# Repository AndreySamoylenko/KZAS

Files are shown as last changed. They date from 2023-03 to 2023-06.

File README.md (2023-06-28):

# О содержании репозитория

В папке [технический журнал](https://github.com/AndreySamoylenko/KZAS/blob/main/технический%20журнал) находятся три документа, в них рассмотрено устройство робота и логика прохождения трассы. 

В файле [Обсуждение системы перемещения.pdf](https://github.com/AndreySamoylenko/KZAS/blob/main/технический%20журнал/Обсуждение%20системы%20перемещения.pdf) рассмотрены некоторые 3D модели и их назначение, а также некоторые аспекты выбора комплектующих.

В файле [Обсуждение системы питания и сенсоров.pdf](https://github.com/AndreySamoylenko/KZAS/blob/main/технический%20журнал/Обсуждение%20системы%20питания%20и%20сенсоров.pdf) представлены сравнения электрических компонентов, и объяснён выбор тех моделей которые вошли в конечную схему. В этом же файле вы можете ознакомиться с логической и принципиальной схемами, которые показывают взаимодействия компонентов и устройство электрической схемы робота.

В файле [Обсуждение системы распознавания препятствий.pdf](https://github.com/AndreySamoylenko/KZAS/blob/main/технический%20журнал/Обсуждение%20систем%20распознавания%20препятствий.pdf) показаны и разобраны некоторые алгоритмы, и объяснены части кода программ из папки [программы](https://github.com/AndreySamoylenko/KZAS/blob/main/программы). В этом документе разобраны только программы отвечающие за распознавание препятствий.

Папка [программы](https://github.com/AndreySamoylenko/KZAS/blob/main/программы) содержит все программы использованные нами в процессе разработки

В папке [видео](https://github.com/AndreySamoylenko/KZAS/blob/main/видео) находится текстовый файл со ссылкой на видео.

Папка  [Фотографии робота](https://github.com/AndreySamoylenko/KZAS/blob/main/Фотографии%20робота) содержит 11 фотографий, 10 фотографий робота и 1 фото команды.

В папке [3D модели](https://github.com/AndreySamoylenko/KZAS/blob/main/3D%20модели) вы можете найти все 3д модели деталей, которые мы печатали.

# Пояснения к программам 

Здесь будет представлено краткое описание программ.

[RobotAPI.py](https://github.com/AndreySamoylenko/KZAS/blob/main/программы/RobotAPI.py) - это класс используемый программой [start_robot.py](https://github.com/AndreySamoylenko/KZAS/blob/main/программы/start_robot.py). Он необходим для загрузки программы на распберри, и получения изображения с камеры по Wi-Fi.

[start_robot.py](https://github.com/AndreySamoylenko/KZAS/blob/main/программы/start_robot.py) - это программа создающая удобный интерфейс для взаимодействия с роботом (фотка). Использование этой программы будет рассмотрено подробно в разделе "подключение к распберри".

[main.py](https://github.com/AndreySamoylenko/KZAS/blob/main/программы/main.py) - это программа, исполняемая микроконтроллером. 
Сама программа выглядит примерно так: 
1) принять сообщение от raspberry  
2) расшифровать его и получить целевой угол сервопривода, скорость мотора и цвет RGB светодиода
3) зажечь светодиод нужным цветом
4) запустить мотор с нужной скоростью
5) повернуть сервопривод на целевой угол
6) повторить

Программы [qualification](https://github.com/AndreySamoylenko/KZAS/blob/main/программы/qualification.py), [final.py](https://github.com/AndreySamoylenko/KZAS/blob/main/программы/final.py) загружаются на raspberry pi с помощью [start_robot.py](https://github.com/AndreySamoylenko/KZAS/blob/main/программы/start_robot.py), и имеют схожую структуру. 

Все их можно разделить на 3 этапа работы (в программе этапы определяются переменной "state"): 

1) ожидание нажатия кнопки (state == 0)
2) прохождение трассы (state == 1)
3) остановка (state == 3)

(когда state == 2 робот проходит последние ползоны, чтобы финишировать в центре) 

На первом этапе raspberry отправляет сообщение "999999999999999999999$", которое pyboard получает и ждет изменения значения, параллельно отправляя показания кнопки. 

Когда кнопка нажата, pyboard отсылает сообщение: "1$". 
raspberry получает это сообщение и начинает движение.   

В [qualification](https://github.com/AndreySamoylenko/KZAS/blob/main/программы/qualification.py), второй этап - прохождение трассы с помощью пропорционально-дифференциального регулятора с двумя датчиками и с параллельным считыванием так называемых перекрёстков (оранжевая и синяя линии). 

ПД регулятор сначала вычисляет отклонение (e=dat1-dat2) исходя из показаний датчиков бортика, а затем на его основе вычисляет управляющее воздействие (u = (e * kp + (e - e_old) * kd))  (e_old - предыдущее отклонение). 

[final.py](https://github.com/AndreySamoylenko/KZAS/blob/main/программы/final.py) работает иначе - в него добавлены функции избегания знаков. 

На кадре появляется большой датчик, который ищет знаки и возвращают их цвет и координаты на кадре, а также, в программе появляется новый ПД регулятор, и если робот замечает знак, то вычисляет новое отклонение относительно этого знака, игнорируя черные линии и используя специальный ПД регулятор для знаков. 
Также для более быстрого прохождения трассы мы добавили функцию разгона, то есть когда робот не видит знаков, его скорость растёт, а когда знак появляется на кадре скорость падает.

Также в папке [программы](https://github.com/AndreySamoylenko/KZAS/blob/main/программы) есть файл [autostart.py](https://github.com/AndreySamoylenko/KZAS/blob/main/программы/autostart.py), в этот файл вы можете импортировать программу, которую робот будет выполнять при запуске.

# Подключение к pyboard 

Для подключения к pyboard необходимо с помощью micro usb кабеля подключить pyboard к компьютеру. После этого в проводнике появится устройство с названием PYBFLASH. 

На этом устройстве будут два файла main.py и boot.py. Файл [main.py](https://github.com/AndreySamoylenko/KZAS/blob/main/программы/main.py) - это та программа, которую будет исполнять pyboard. 

Вы можете скопировать её в свою среду разработки и изменить, если это необходимо, после этого вам нужно заменить файл [main.py](https://github.com/AndreySamoylenko/KZAS/blob/main/программы/main.py) в папке PYBFLASH на отредактированный, и после того как погаснет красный светодиод нужно будет нажать на кнопку RESET (RST). 
После этого pyboard перезагрузится и начнёт выполнение программы [main.py](https://github.com/AndreySamoylenko/KZAS/blob/main/программы/main.py)
  
# Подключение к raspberry pi 

Сначала вам нужно включить питание робота (или подключить питание распберри отдельно) и подождать какое-то время, это нужно для того чтобы на распберри запустилась операционная система, и включилась точка доступа. 
После этого ищем сеть нашей raspberry и подключаемся к ней.

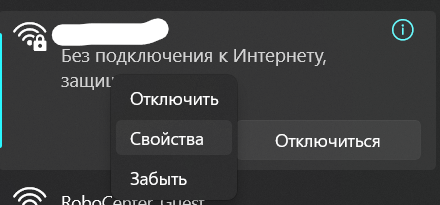
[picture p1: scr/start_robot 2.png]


Нажимаем "свойства" и ищем пункт "IPv4".

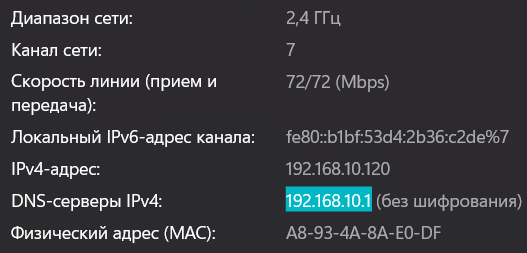
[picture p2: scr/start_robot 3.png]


После этого копируем это IP адрес и вставляем его в [start_robot.py](https://github.com/AndreySamoylenko/KZAS/blob/main/программы/start_robot.py) как на фото.

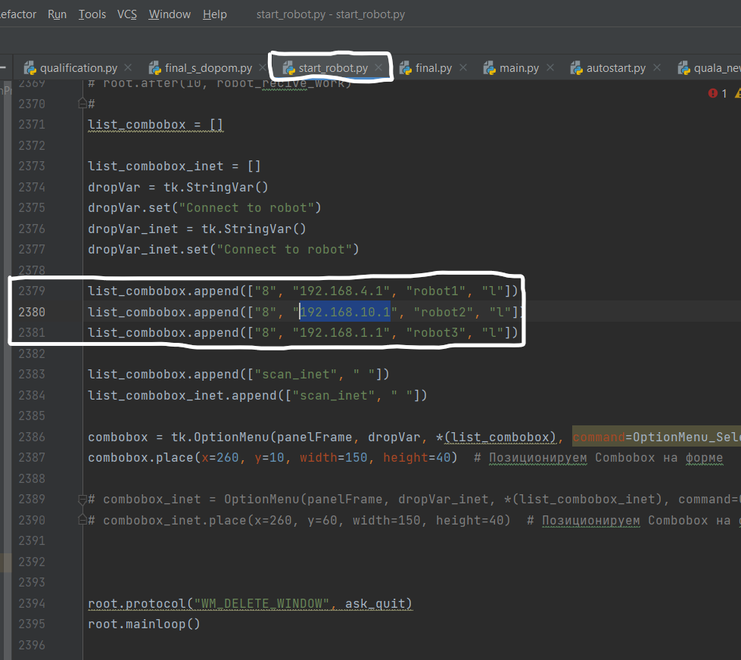
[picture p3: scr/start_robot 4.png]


здесь же можно изменить подпись, которая будет отображаться в выпадающем меню.

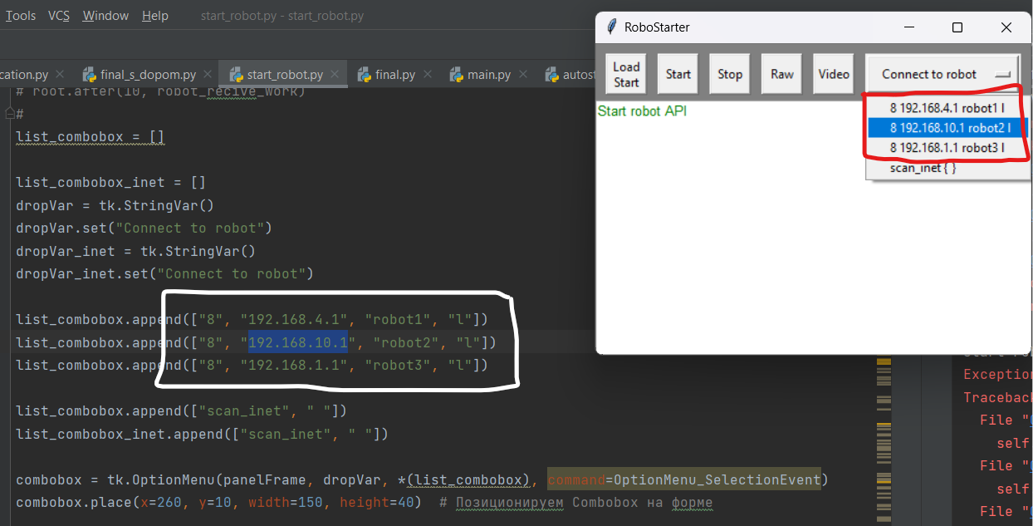
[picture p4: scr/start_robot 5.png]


После этого перезапускаем [start_robot.py](https://github.com/AndreySamoylenko/KZAS/blob/main/программы/start_robot.py), выбираем нашего робота и нажимаем кнопку "load start" и в окне с файлами выбираем нужный. 
 
Ваша программа будет загружена и если на pyboard горит желтый светодиод, значит pyboard успешно получает сообщения от raspberry. 

После того, как вы выбрали программу в [start_robot.py](https://github.com/AndreySamoylenko/KZAS/blob/main/программы/start_robot.py), ее можно запустить, нажав кнопку на роботе. 
 
Но если вы выключили и включили робота, то ваша программа не запустится. 
 
В этом случае запускается программа, которая импортирована в [autostart.py](https://github.com/AndreySamoylenko/KZAS/blob/main/программы/autostart.py). 
 
Поэтому вы можете импортировать нужную программу в [autostart.py](https://github.com/AndreySamoylenko/KZAS/blob/main/программы/autostart.py) и вам не нужно будет перезапускать программу через [start_robot.py](https://github.com/AndreySamoylenko/KZAS/blob/main/программы/start_robot.py). 

# Если что-то пошло не так 

Если вы столкнулись с трудностями, или робот не работает, то рекомендуется выполнить следующие действия. 
 
Если вы не можете подключиться к роботу через [start_robot.py](https://github.com/AndreySamoylenko/KZAS/blob/main/программы/start_robot.py) перечитайте раздел "подключение к raspberry pi". 

Если робот работает неправильно, проверьте напряжение на вольтметре. Если оно ниже 9 вольт, немедленно меняйте аккумуляторы (рекомендуется менять аккумуляторы, как только напряжение упадет до 10,5 вольт).

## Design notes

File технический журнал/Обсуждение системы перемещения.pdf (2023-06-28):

## Обсуждение системы перемещения

Прежде всего стоит отметить, что мы используем готовые мосты от радиоуправляемой машинки (https://sl.aliexpress.ru/p?key=Ep6PZ9z), но мы доработали их и добавили некоторые детали для лучшей работы и более простого крепления к остальным комплектующим. Удобство готовых мостов в том, что они содержат в себе редукторы на каждом колесе и передачу ось-колесо.

Но есть и минусы в готовой раме. Во-первых, подвеска оказалась слишком слабой для
несения всей электроники, особенно аккумуляторов. Эту проблему мы решили
добавлением проставок (файл “spacer.stl”).

Во-вторых, рулевой мост был спроектирован неверно, это выражалось в том, что во время поворота внутреннее колесо поворачивалось меньше, чем внешнее, и тем самым мешало повороту. Мы решили это добавлением некоторых деталей в рулевую
систему, если кратко, то мы вынесли крепления рулевой тяги на внешнюю сторону с
помощью детали “steering_knukle.stl”.

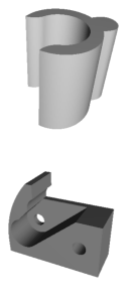
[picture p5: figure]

Вследствие этого оригинальная деталь нам уже не подходила, и мы напечатали свою (“tie_rod.stl”), также мы напечатали деталь-переходник между качалкой сервопривода и новой рулевой тягой (“steering_shaft.stl”).

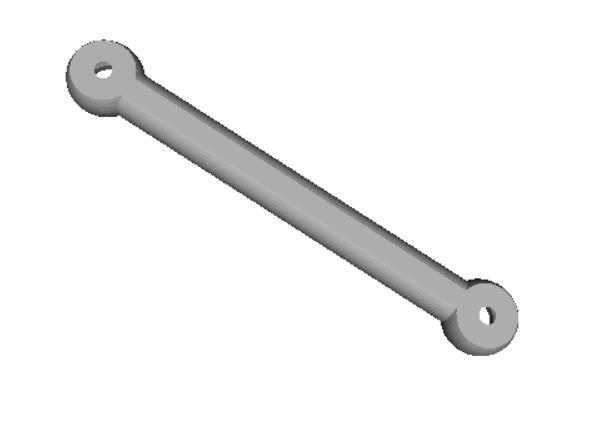
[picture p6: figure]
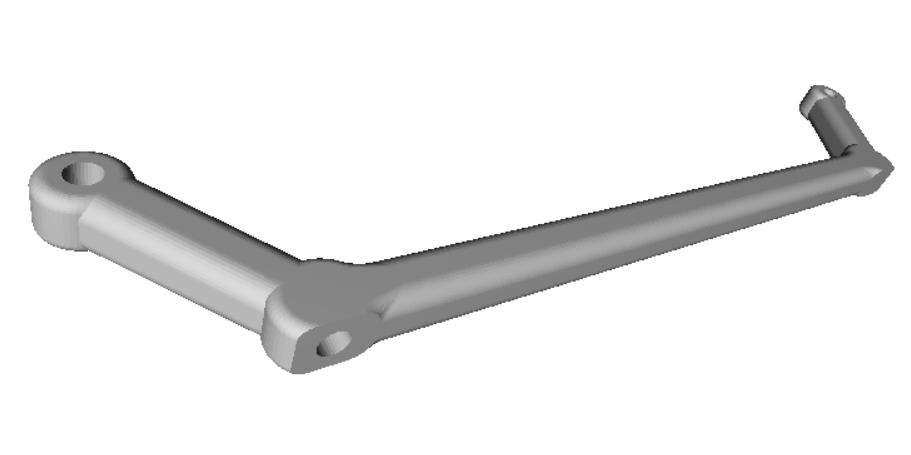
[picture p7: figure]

steering_shaft.stl | tie_rod.stl

Тип подвески

Вариантов подвески было два: независимая и зависимая.

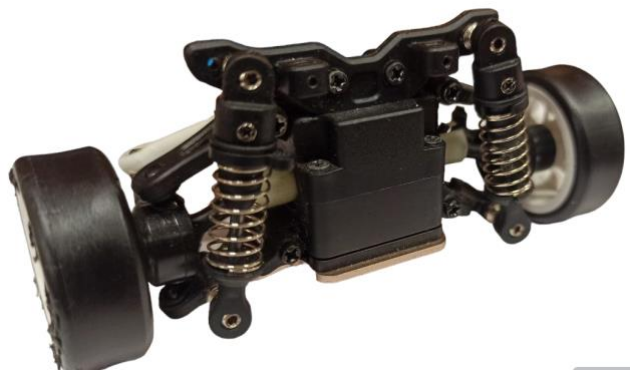
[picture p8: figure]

Независимая подвеска считается более подходящей для ровных дорог и лучше управляется на них, но конкретно наша рама не очень подходила по габаритам, и имела неудобные крепления колёс.

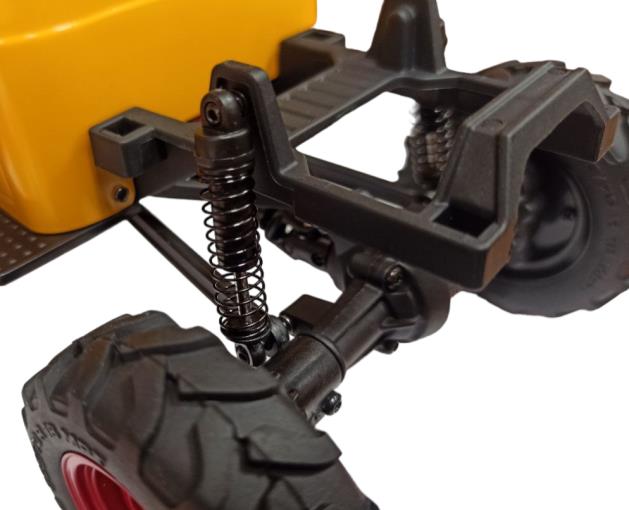
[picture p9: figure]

Рама с зависимой подвеской оказалась удобнее как по габаритам, так и по креплениям. Колёса крепятся к ней на винты М3, а шарниры подвески имеют резьбу М2. Эти два фактора в большей степени повлияли на наш выбор, так как благодаря им можно легко спроектировать свой корпус со всеми необходимыми креплениями, а также свои диски для колёс.

В итоге мы выбрали раму с зависимой подвеской.

Колёса и шины

Фото

Наименование | Колёса от машинки | LEGO 43.2x26 | LEGO 43.2x22 | LEGO 43.2x14
Описание | Имеют довольно большой диаметр в 60 миллиметров, что добавит лишней скорости, кроме того, имеют крайне мягкие, но скользкие шины, рассчитанные на бездорожье, и имеющие сцепление только на неоднородном покрытии. | Из-за округлости страдает сцепление, но меньший диаметр позволяет не развивать слишком большую скорость. (что относится и к остальным шинам) | Довольно плоский рельеф и большая ширина не обеспечивают достаточного давления. | Небольшая ширина и змеевидный рельеф давят на поле довольно сильно, а следовательно, дают достаточное сцепление.

В итоге колёса от машинки - скользкие, 43.2 на 26 - круглые и слишком широкие, 43.2 на 22 - плоские и тоже широкие, 43.2 на 14 - вариант не оптимальный, но лучший из имеющихся. При выборе мы учитывали, что более широкие колёса увеличивают максимальный радиус при повороте, поэтому мы выбрали самые узкие колёса.

Мотор

Фото

Напряжени е питания | 6 вольт | 6 вольт | 6 вольт | 12 вольт | 12 вольт | 12 вольт
Ток без нагрузки | 0.05 ампер | 0.04 ампера | 0.05 ампера | 0.44 ампера | 0.75 ампер | 0.63 ампера
Пусковой ток | 0.20 ампер | 0.28 ампер | 0.53 ампера | 1.21 ампер | 1.68 ампер | 1.10 ампер
Обороты в минуту | 300 | 300 | 1000 | 980 | 2000 | 750

С редукторами на колёсах, встроенными в мосты, и мотором с оборотами до 1000 скорость робота недостаточна. Поэтому мы установили мотор на 2000 оборотов и 12 вольт.

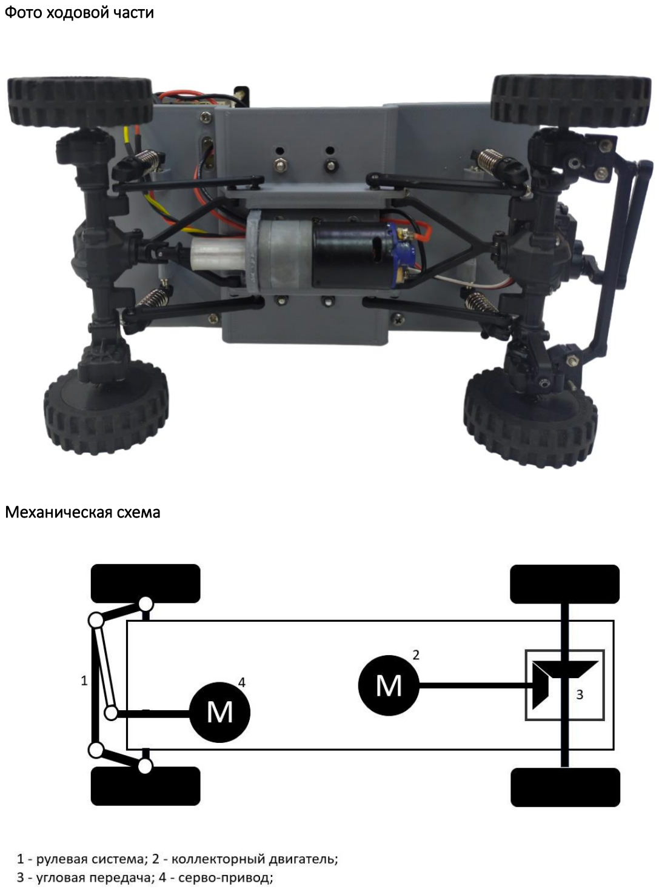
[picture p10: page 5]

Фото ходовой части

Механическая схема

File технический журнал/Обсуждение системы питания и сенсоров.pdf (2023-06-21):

## Обсуждение системы питания и сенсоров

### Система питания

Система представлена тремя последовательно соединёнными литий-ионными аккумуляторами типа 18650, стабилизатором на 5 вольт и потребителями (см. Дополнительные материалы/электрическая схема).

Для начала нужно объяснить выбор аккумуляторов

Фото

Тип | Li-Po | Li-ion 18650 | Li-ion 14500 | Ni-MH АА
Средняя ёмкость на батарею | 2600 мАч | 3100 мАч | 1000 мАч | 2200 мАч
Напряжение на батарею | 3–4.2 вольта | 3–4.2 вольта | 3–4.2 вольта | 1–1.4 вольта
Токоотдача | 60–120 ампер | 3–6 ампер | 2–4 ампера | 2–4 ампера

Мы используем именно литий-ионные аккумуляторы по ряду причин: они имеют соотношение емкости и массы больше, чем у других типов аккумуляторов, и довольно большой пиковый ток; три аккумулятора подключённые последовательно дают напряжение 12 вольт, такое же рабочее напряжение имеет мотор, который мы используем (при использовании другого мотора необходимо либо изменить количество аккумуляторов, либо добавить в цепь питания драйвера понижающий DC-DC преобразователь). Мы используем батареи формфактора 18650 так как это один из популярных типов аккумуляторов и для них существуют удобные холдеры, также они имеют большую емкость и токоотдачу чем никель-металлгидридные АА и литий-ионные аккумуляторы 14500. Все эти преимущества есть и у литий-полимерных аккумуляторов, но у них ниже ёмкость, и не очень удобный способ зарядки.

12 вольт от аккумуляторов через ключ идут на стабилизатор и на мотор через драйвер. Параллельно аккумуляторам подключён вольтметр для контроля заряда.

5 вольт со стабилизатора идут на микроконтроллер(pyboard), компьютер(raspberry) и сервопривод.

Питание raspberry происходит через обрезанный провод type-C, так как на этот порт установлен фильтр питания.

### Стабилизатор

Три основных варианта стабилизаторов, которые мы рассматривали, представлены в таблице ниже.

Фото

Наименование | DD2712SA | LM2596S | LM2596S с вольтметром
Габариты | 15.4х25.0 | 21.5х43.0 | 36х66
Входное напряжение | 5-27В | 3-40В | 3-40В
Выходное напряжение | 5-12В (фиксированное) | 1.5-35В (настраиваемое) | 1.5-35В (настраиваемое)
КПД (средний) | 77–92% | 92% и ниже | 92% и ниже
Максимальный ток при длительной работе | 2.5А | 2А | 2А
Максимальный импульсный ток | 3.5А | 3А | 3А

Как можно видеть из таблицы все эти DC-DC преобразователи подходят по диапазонам напряжений и самые принципиальные различия среди них — это различия в размере. DD2712SA в этом плане самый подходящий вариант, у него отсутствуют большие конденсаторы и клеммы, он отличается малым размером и возможностью пайки на плату. Также он имеет фиксированное напряжение, что довольно удобно, так как нам не нужно никакое другое напряжение кроме 5 вольт, кроме того, исключается возможность случайно сбить установку напряжения.

### Система сенсоров

Из сенсоров мы используем только камеру, подключаемую к raspberry, так как камера даёт достаточно информации об окружении робота. Камера снимает окружение и на каждом кадре мы выделяем по 4 области интереса, или же 4 датчика, два датчика бортиков, один датчик поворота и один большой датчик знаков. Информация о датчиках и их принципе работы вы можете прочитать в обсуждении системы распознавания препятствий.

Компьютер и камера

В качестве одноплатного компьютера мы выбрали raspberry pi 4 B+. Это простой в использовании, и очень популярный и мощный компьютер.

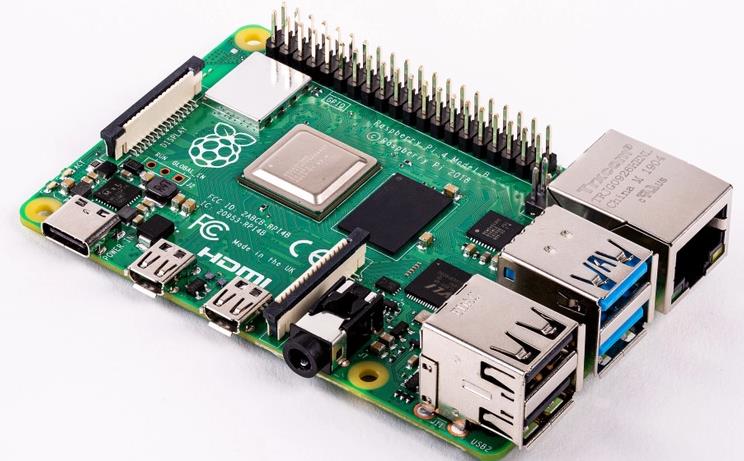
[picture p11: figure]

### Камера

Существует несколько камер, совместимых с raspberry pi, различающихся по характеристикам:

Фото

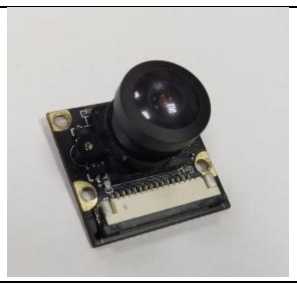
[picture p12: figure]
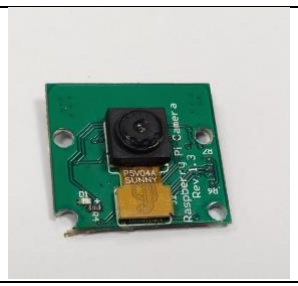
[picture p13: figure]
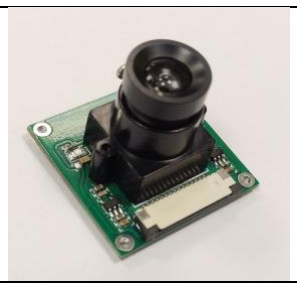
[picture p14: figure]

Название | Камера от Wave Share | RPi Camera rev. 1.3 | RPi Camera (B) rev. 2.0
Фокус | Настраиваемый | Фиксированное | Настраиваемый
Укол диагонали | 200 градусов | 72.4 градуса | 75.7 градусов

Мы выбрали чёрную камеру от Wave Share только из-за большого угла обзора, он позволяет видеть бортик даже находясь почти за ним. Это позволяет правильно оценивать положение робота относительно окружения.

### Остальные электрические компоненты

Электрические компоненты, не входящие в схему питания, будут представлены здесь.

Микроконтроллер | в качестве микроконтроллера мы используем Pyboard 1.1v. Этот микроконтроллер имеет высокую тактовую частоту, удобные логические уровни в 3.3 вольта, совпадающие с логикой raspberry, разрядность ШИМ в 16 бит и небольшие габариты. Также Pyboard программируется на python как и raspberry, что очень удобно при разработке.
Драйвер мотора | Мы выбрали TB6612FNG, так как у него подходящее рабочее напряжение (до 13 вольт), достаточный предельный ток (2.4 А) и малые габариты (приблизительно 20х20 мм).
Кнопка | Мы используем сенсорную кнопку на чипе ttp223
RGB светодиод | У нас готовый модуль с резисторами
Ключ | Находится между плюсом аккумуляторов и схемой
Конденсатор | Электролитический 1000 микрофарад 16 вольт
Вентиляторы х2 | 30х30 мм (для распберри ). С их помощью мы охлаждаем процессор распберри и драйвер моторов.

### Дополнительные материалы

При желании вы можете заменить некоторые или все рассмотренные выше комплектующие. В таком случае вам будут полезны логическая и принципиальная схемы. Они приложены ниже и отражают устройство робота.

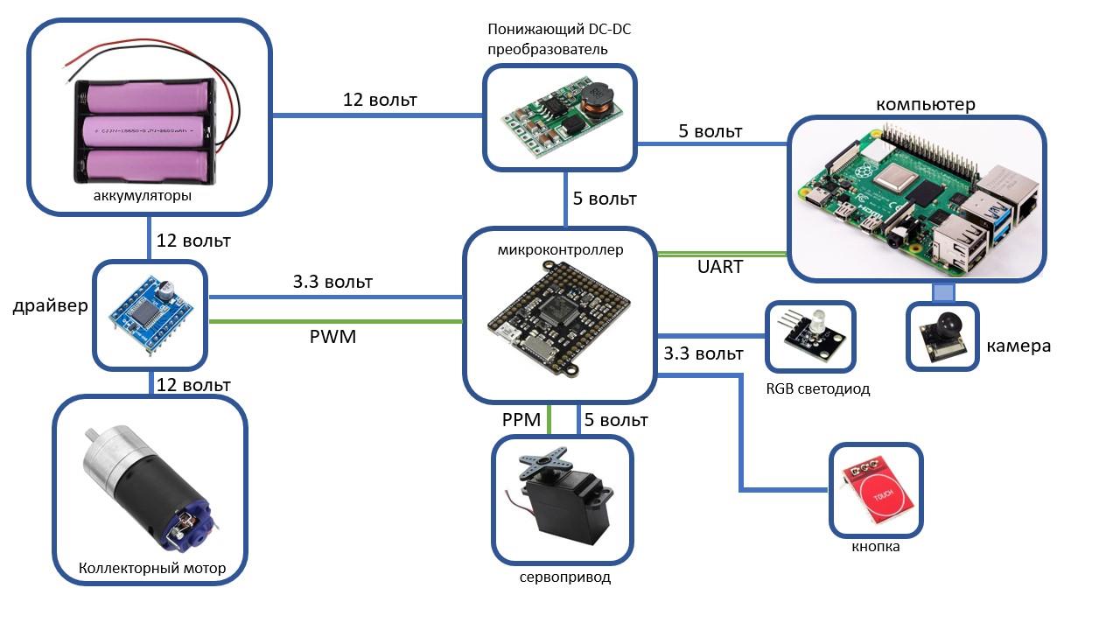
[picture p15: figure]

Логическая схема

На логической схеме описаны все взаимодействия между компонентами, также на этой схеме подписаны компоненты в общем, а не модели или брэнды, таким образом мы показываем возможность замены компонентов, например, сенсорной кнопки на обычную тактовую кнопку, или пайборда на другой микроконтроллер. Таким образом, вы можете заменить любой элемент схемы, но понадобится производить изменения в программе и схемотехнике.

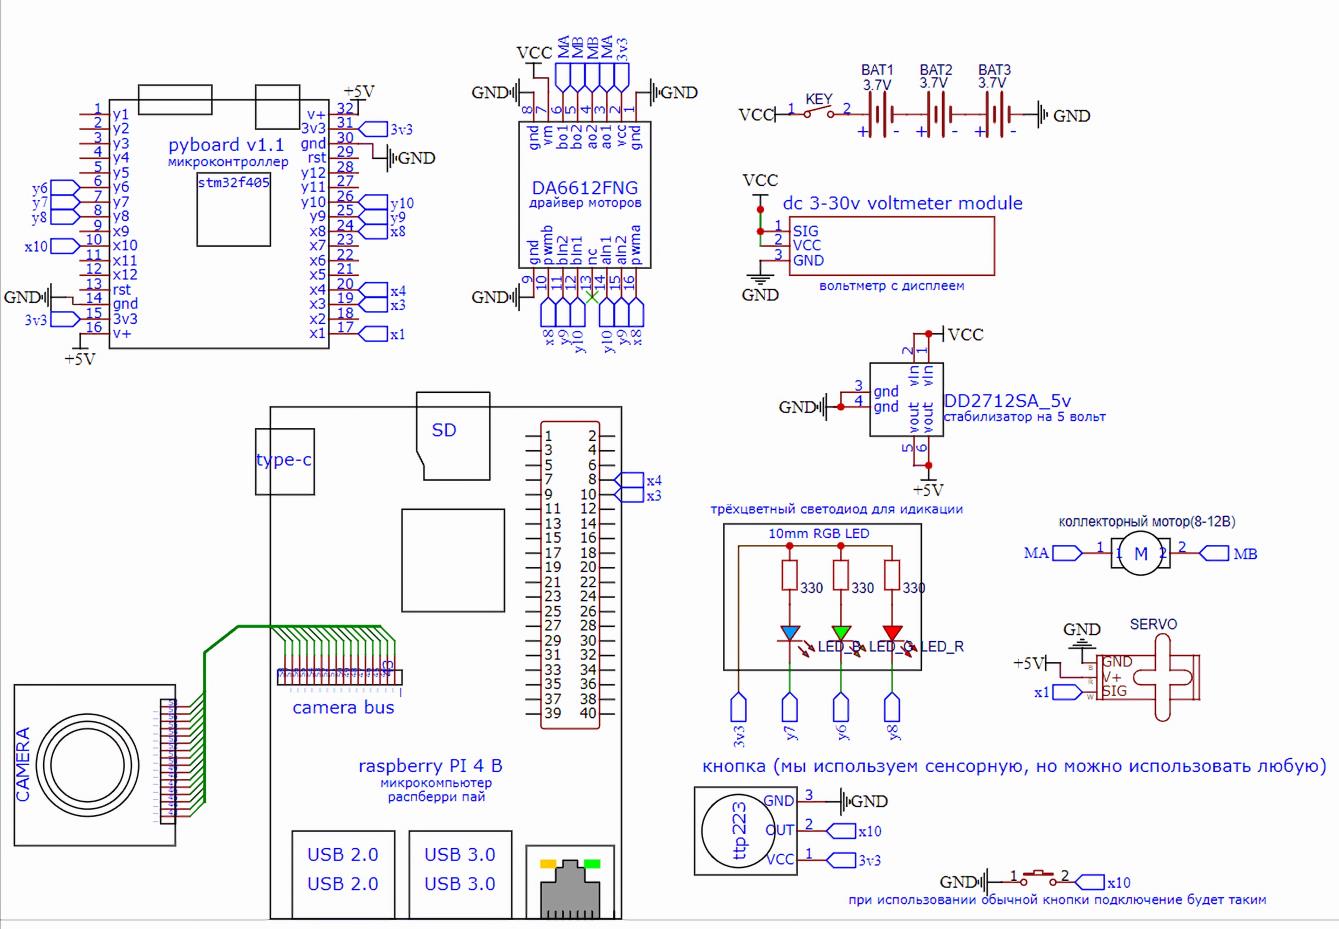
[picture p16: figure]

Электрическая схема
Эта схема отображает принцип, по которому мы разводили плату, и фактически является более подробной версией логической схемы.

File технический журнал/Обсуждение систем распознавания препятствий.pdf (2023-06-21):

## Обсуждение систем распознавания препятствий

### Квалификация

Для начала следует взглянуть на поле глазами робота

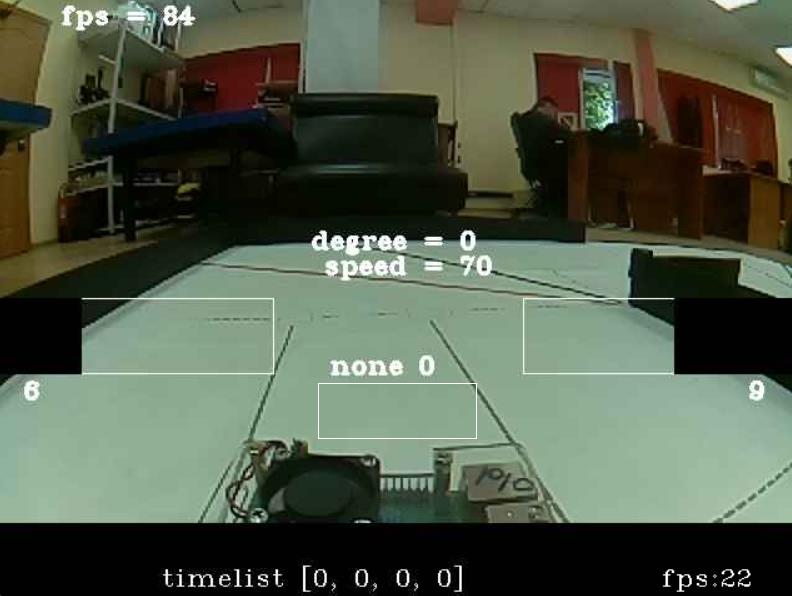
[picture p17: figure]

На этом фото мы можем видеть поле, телеметрию (текст на экране), а также прямоугольники. Эти прямоугольники — это графическое отображения областей интереса. Они очерчивают границы области поиска тех или иных объектов, например, два прямоугольника по бокам кадра очерчивают границы областей поиска бортиков, а небольшой прямоугольник по центру — область поиска синей и оранжевой линии. В дальнейшем для простоты и краткости область интереса и прямоугольник мы объединим в понятие датчик. То есть на кадре присутствует 3 датчика: 2 датчика бортика и один датчик перекрёстков (перекрёстком называется синяя или оранжевая линия, в зависимости от направления движения).

### Датчики

Датчики нужны для того, чтобы определить позицию объекта (бортика, знака, линии) по цвету в модели HSV. Все датчики устроены похожим образом и имеют базовый набор действий:

1)Скопировать часть кадра 2) перевести полученное изображение в цветовую модель HSV 3) создать маску 4) найти на этой маске контуры 5) найти наибольший контур 6) передать его координаты.

Создание маски — это процесс создания массива нулей и единиц на основе изображения в цветовом пространстве HSV и диапазона значений. Алгоритм создания таков:

Если цвет пикселя на исходном изображении входит в данный диапазон, то пиксель с такими же координатами на маске становится белым, иначе пиксель будет чёрным.

Наглядная демонстрация создания маски

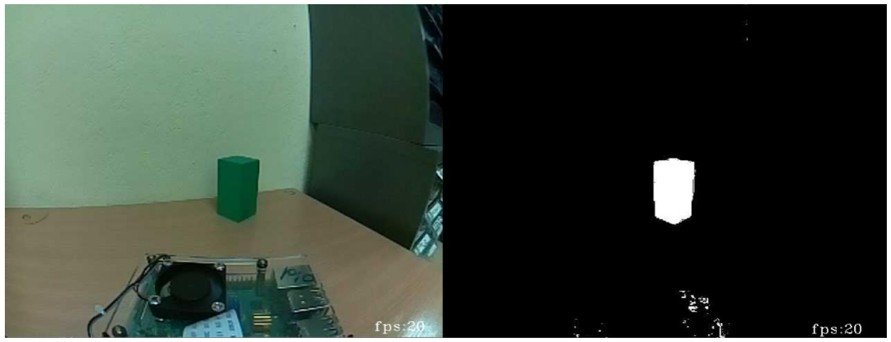
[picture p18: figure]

## Алгоритм движения

После разбора основных составляющих можно перейти к общему алгоритму движения, он будет представлен ниже в форме псевдокода.

Получить кадр с камеры

Если робот находится в фазе движения: Обработать датчики бортиков
ПД регулятор
Обработать датчик перекрёстка

Если робот находится в фазе активного торможения:
Если с перехода в фазу активного торможения прошло менее 100 миллисекунд: скорость = -100
Иначе:
перейти в фазу остановки

Если робот находится в фазе остановки: Скорость = 0
Угол поворота = 0

Если количество перекрёстков равно 12 и флаг опущен: Поднять флаг
Засечь время
Количество перекрёстков = 13

Если с момента 12-го перекрёстка прошло больше времени чем нужно для преодоления половины зоны:
Перейти в фазу активного торможения
Засечь время
Опустить флаг

Передать значение угла поворота из ПД регулятора на микроконтроллер

В данном фрагменте упущены некоторые части кода, не влияющие на прохождение траектории, такие как индикация или подсчёт кадров в секунду.

Но если рассматривать более подробно, то для начала следует посмотреть на код программы. wait_for_key()
while 1:
frame = robot.get_frame(wait_new_frame=1)

if state == 1:
red, green, blue = 0, 0, 0 detect_line_pro()
pd_regulator(dat1, dat2)
search_cross()
if search_cross_time + 0.5 > time.time(): if color_line == 'orange':
red = 84
green = 54
if color_line == 'blue':
blue = 80
green = 20

Этот код мы взяли из программы qualification.py и убрали все комментарии. Тут, очевидно, не вся программа, это только фаза движения, которая, в прочем, представляет собой весь алгоритм.

wait_for_key() — это функция ожидания нажатия кнопки, она посылает на микроконтроллер сообщение '999999999999999999999$', которое свидетельствует о том, что распберри запустилась, и начала выполнять программу. Параллельно происходит чтение сообщений с микроконтроллера, которые содержат всего одну цифру, ноль либо единицу. Ноль — кнопка не нажата, один — кнопка нажата. Как только приходит сообщение о нажатой кнопке, распберри выходит из этой функции.

frame = robot.get_frame(wait_new_frame=1) — этой строчкой мы получаем снимок с камеры, который мы будем использовать в дальнейшем.

if state == 1: — переменная state отвечает за режимы работы робота, 1 — выполнение задания, 2 — активное торможение, 3 — остановка.

red, green, blue = 0, 0, 0 — эти три переменные отвечают за цвета RGB светодиода.

detect_line_pro() — эта функция отвечает за работу датчиков бортиков, но не отрисовывает их на экране. Внутри у неё не так много кода, потому что она использует две другие функции и упрощает работу с ними. Её задача просто приравнять глобальные переменные dat1 и dat2, к показаниям датчиков.

pd_regulator(dat1, dat2) — эта функция обыкновенный пропорционально-дифференциальный регулятор с некоторыми дополнениями в виде частных случаев, в роде: если левый датчик равен нулю, следовательно мы на повороте и только что проехали угол, следовательно сейчас необходимо сделать поворот влево.

search_cross() — эта функция занимается поиском перекрёстков на соответствующем датчике. Эта же функция записывает время зон в список.

А далее идет индикация обнаружения перекрёстков.

И это весь алгоритм движения, дальше только активное торможение и остановка.

## Финал

Финальный заезд отличается от квалификационного только знаками на поле, соответственно, программа будет отличаться только алгоритмами, связанными со знаками.

Знаки мы определяем по HSV с помощью датчика, как и остальные объекты.

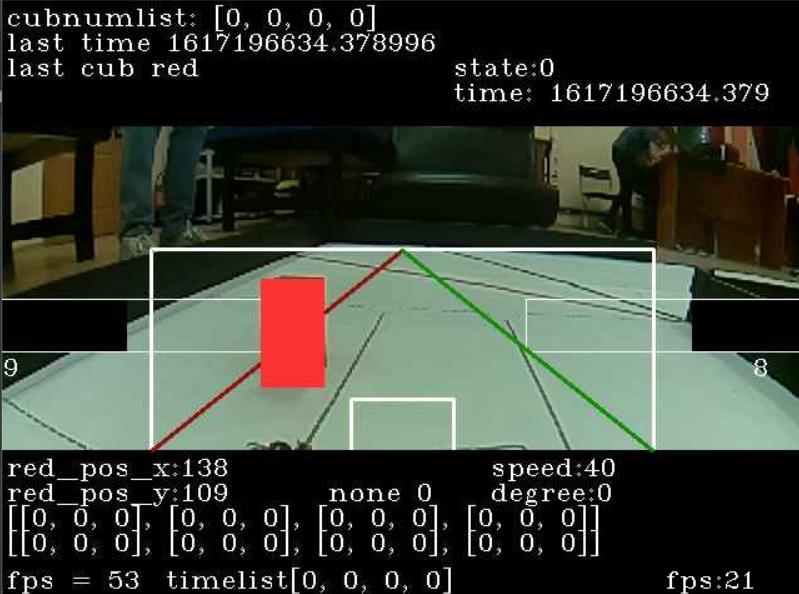
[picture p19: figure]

Экран финального заезда отличается от квалификационного только датчиком знаков. Так как знаки могут быть где угодно и на любом расстоянии от робота, датчик должен быть довольно большим. Когда робот замечает знак, он начинает ориентироваться только по нему, игнорируя бортики. Для этого у нас есть отдельная функция с ПД регулятором (pd_regulator_cube). Эта функция отличается от обычного ПД регулятора тем, что в ней ошибка высчитывается исходя из перспективы, которая изображена зелёной и красной линиями на экране. Перспектива подразумевает, что в зависимости от расстояния до знака мы должны занимать разные позиции в пространстве относительно него. Например, если красный знак на камере высоко, то он достаточно далеко от робота (рис. 1), и чтобы к нему правильно подъехать, нужно фиксировать его по середине кадра, а если он низко на камере, то есть находится возле робота (рис. 2), то, чтобы его не сбить, робот должен находиться максимально справа. То есть существует зависимость положения знака по X координате от положения знака по Y координате, и эту зависимость можно представить в виде функции: x = k * y + b, а в нашем случае для красного это - x = 240 – y * 1.23, и для зеленого - x = 160 + y * 1.23. И это значение X - это установка, к которой стремится ПД регулятор.

Рис. 1 | Рис. 2

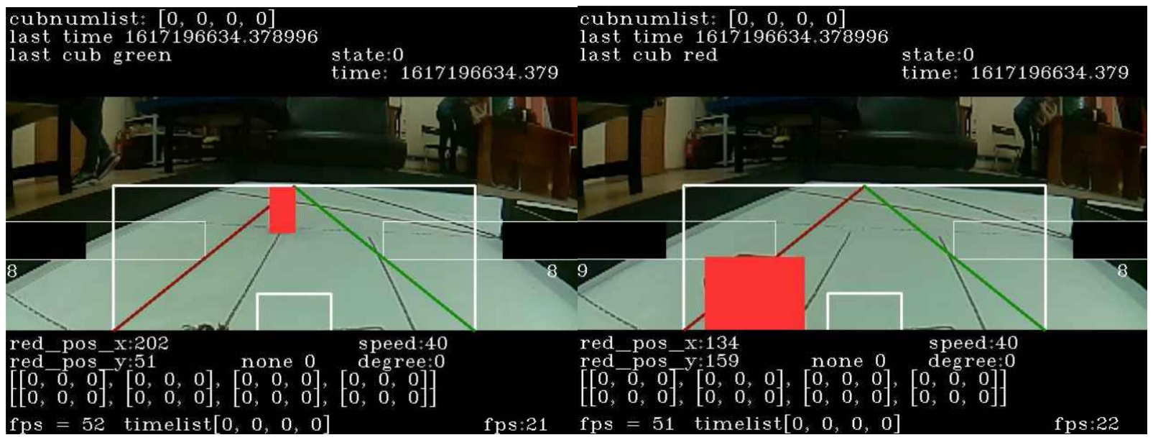
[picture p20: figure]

Алгоритм фазы движения финального заезда выглядит так:

Обработать датчики знаков

Если ни одного знака не обнаружено:

Обработать датчики бортиков

Двигаться с помощью ПД регулятора

Если знак, который нужно объезжать с внешней стороны, пропал менее 400 миллисекунд назад:

Совершить поворот в сторону движения

#это сделано для того, чтобы быстро вернуться на траекторию

Иначе если есть зеленый и он ближе:

Двигаться с помощью ПД регулятора для знаков

Иначе

Двигаться с помощью ПД регулятора для знаков

Обработать датчик перекрёстков

А фазы активного торможения и остановки абсолютно идентичны с квалификацией

Далее будет представлен фрагмент кода, и более подробный его разбор.

if state == 1: # езда
red, green, blue = 0, 0, 0
if search_cross_time + 0.5 > time.time():
if color_line == 'orange': # если цвет перекрёстка оранжевый зажечь оранжевый red = 60
green = 50
if color_line == 'blue': # если цвет перекрёстка синий зажечь синий
blue = 80
green = 20
green_pos = cube_g()
red_pos = cube_r()
green_pos_x = green_pos[0] - 1 green_pos_y = green_pos[3] red_pos_x = red_pos[2] + 1
red_pos_y = red_pos[3]

if green_pos_x == 0 and red_pos_x == 0: # если нет знаков detect_line_pro() # ищем бортики
pd_regulator(dat1, dat2, kp, kd)

if cube_green_exist + 0.4 > time.time() and color_line == 'orange': degree = -50
if cube_red_exist + 0.4 > time.time() and color_line == 'blue': degree = 50

elif green_pos_x > 0 and green_pos_y > red_pos_y:
cube_color = "Green"
cube_exist_tim = time.time()
if color_line == 'blue':
b_g = 150
elif color_line == 'orange': b_g = 180
else:
b_g = 160
pd_regulator_cube(green_pos_x, (b_g + green_pos_y * 1.23)) red, green, blue = 0, 100, 20

else: # если есть красный
cube_color = "Red"
cube_exist_tim = time.time() if color_line == 'blue':
b_r = 230
elif color_line == 'orange': b_r = 220
else:
b_r = 240
pd_regulator_cube(red_pos_x, (b_r - red_pos_y * 1.23)) red, green, blue = 100, 0, 0

search_cross()

Начало кода в программе для финала взято из квалификации, где мы, в зависимости от цвета перекрёстка, зажигаем RGB светодиод, если перекрёсток был замечен менее 500 милисекунд назад.

Далее мы объявляем переменные: green_pos, red_pos, green_pos_x, green_pos_y, red_pos_x и red_pos_y.

cube_g() и cube_r() – это функции, которые определяют положение зелёного и красного знаков на камере и возвращают их координаты. То есть в списках green_pos и red_pos находятся координаты зелёного и красного знаков, а в переменных green_pos_x, green_pos_y, red_pos_x и red_pos_y находятся координаты нижнего левого угла зелёного знака и координаты правого нижнего угла красного знака.

Затем идет условие, что если знаков не обнаружено, то робот едет по обычному ПД – регулятору. В это условие встроено ещё два условия, для красного и зеленого знаков. Они нужны для того, чтобы вернуться на траекторию после объезда знака с внешней стороны.

Потом идет ещё одно условие. Если робот замечает зелёный знак, и он ближе красного, то мы:

1. Присваиваем переменной cube_color значение "Green";
2. Засекаем таймер;
3. Устанавливаем коэффициент “b” прямой в зависимости от цвета перекрёстка (коэффициент нужен для объезда знака);
4. Объезжаем знак по специальному ПД регулятору pd_regulator_cube() (ошибка считается исходя из перспективы);
5. Зажигаем RGB cветодиод зелёным цветом.

Иначе, если ни одно из вышеперечисленных условий не сработало, то перед роботом красный знак и мы:

1. Присваиваем переменной cube_color значение "Red";
2. Засекаем таймер;
3. Устанавливаем коэффициент “b” прямой в зависимости от цвета перекрёстка (коэффициент нужен для объезда знака);
4. Объезжаем знак по специальному ПД регулятору pd_regulator_cube() (ошибка считается исходя из перспективы);
5. Зажигаем RGB cветодиод красным цветом.

В конце, как и в квалификации, ищем перекрёсток с помощью функции search_cross().

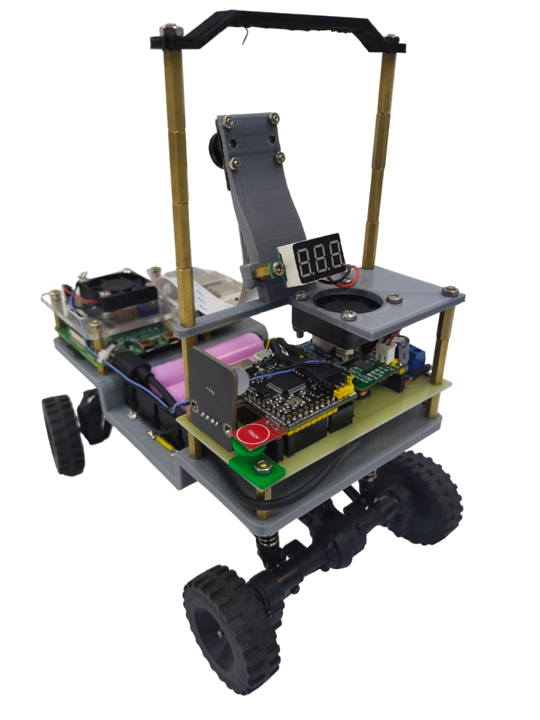
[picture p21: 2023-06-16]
Фотографии робота/с угла слева сзади.png

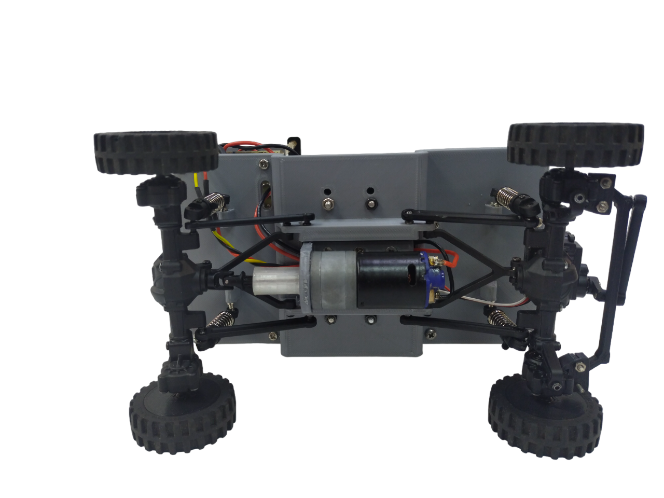
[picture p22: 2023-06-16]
Фотографии робота/снизу.png

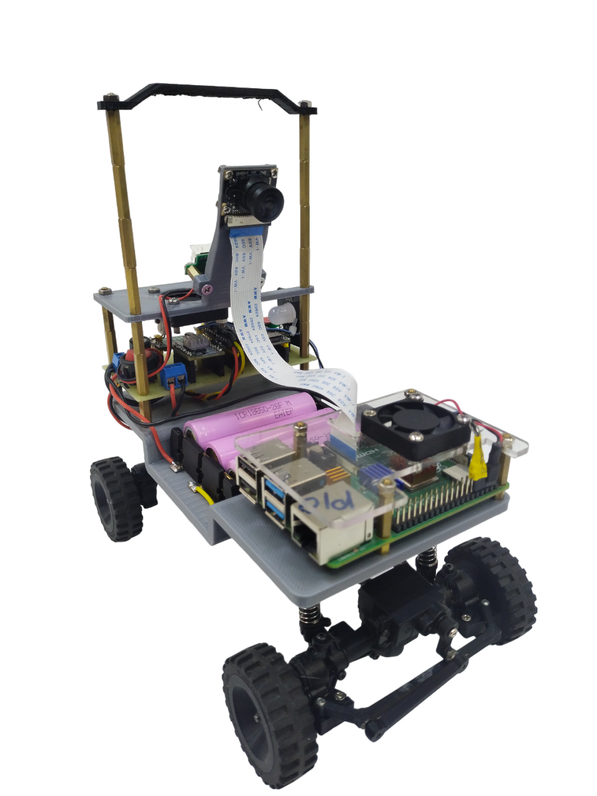
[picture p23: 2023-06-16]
Фотографии робота/с угла справа сверху.png

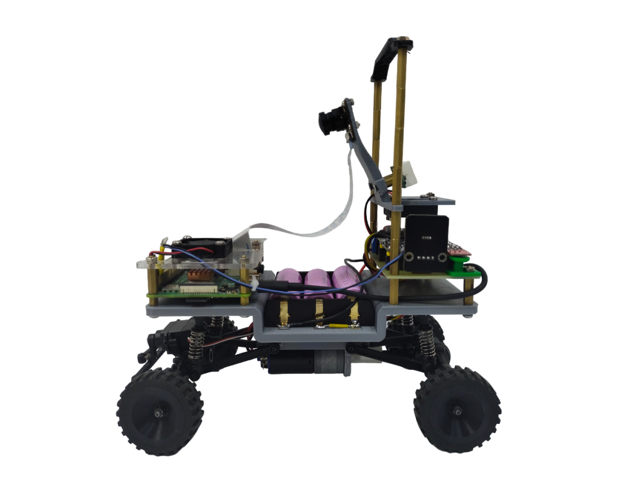
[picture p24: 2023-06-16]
Фотографии робота/слева.png

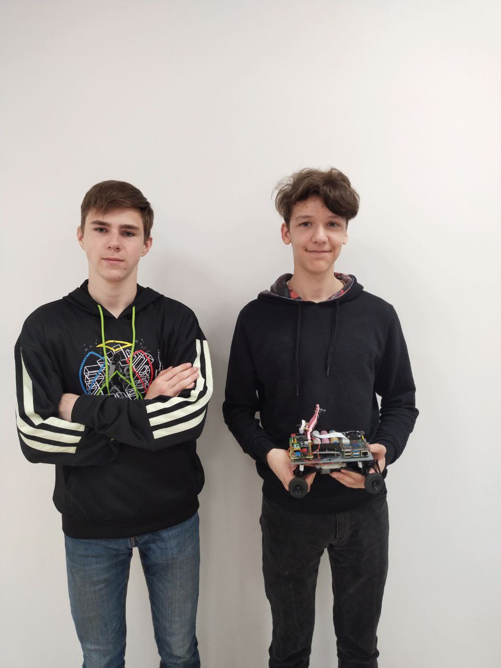
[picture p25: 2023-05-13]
Фотографии робота/фото команды.jpg

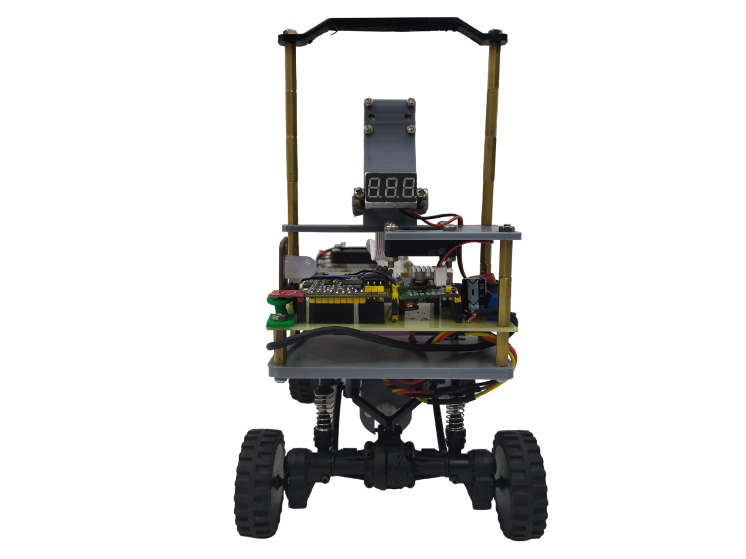
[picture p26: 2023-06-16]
Фотографии робота/сзади.png

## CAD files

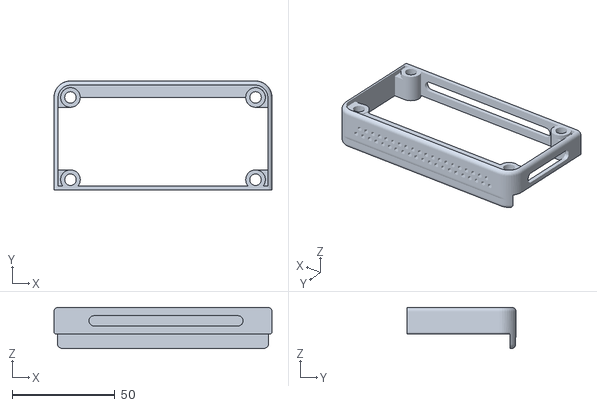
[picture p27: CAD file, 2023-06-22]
3D модели/back_bumper.stl
106.0 x 53.0 x 20.0

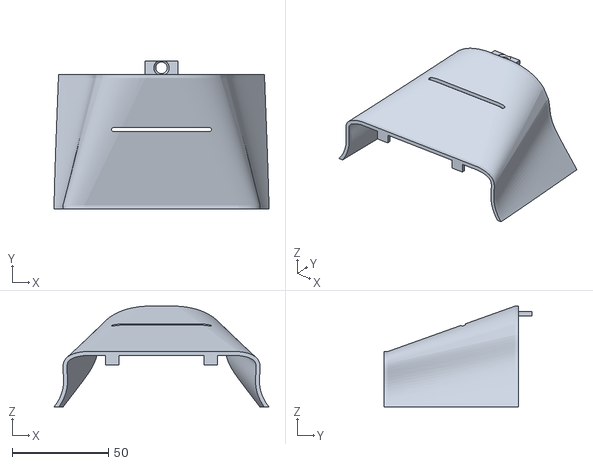
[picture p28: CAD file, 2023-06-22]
3D модели/mid_box.stl
111.7 x 77.0 x 52.3

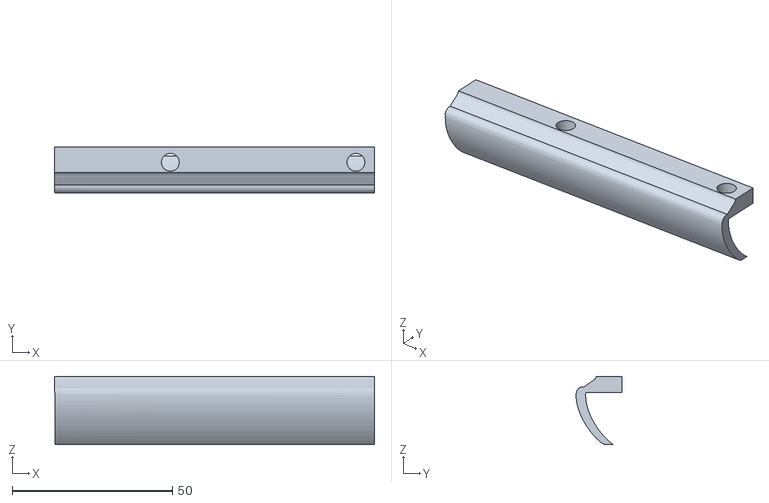
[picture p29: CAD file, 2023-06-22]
3D модели/front_bumper.stl
100.0 x 14.3 x 21.3

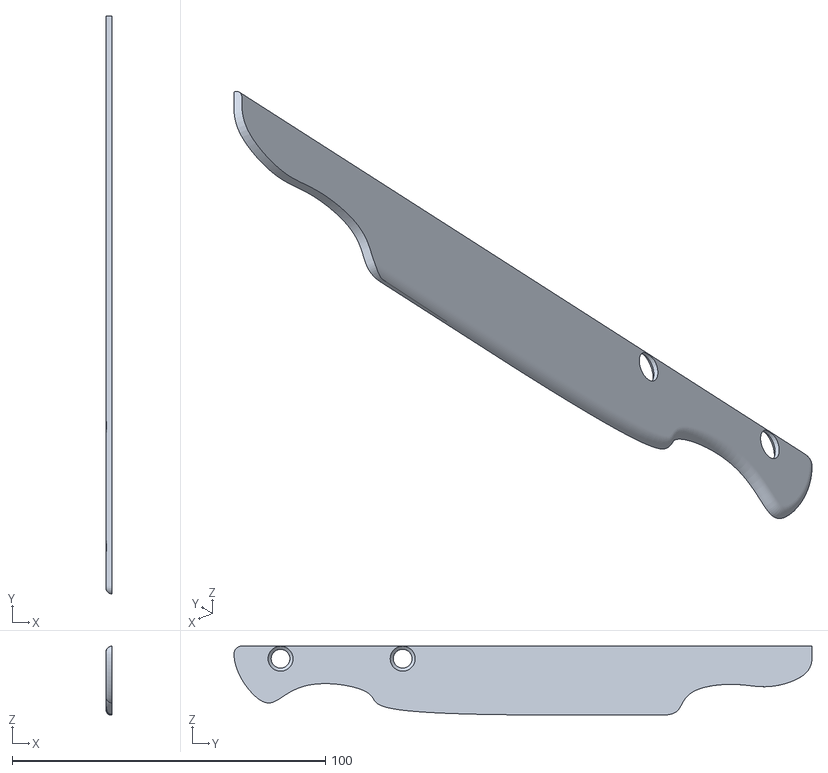
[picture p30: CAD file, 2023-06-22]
3D модели/bok_left.stl
2.00 x 184.6 x 22.0

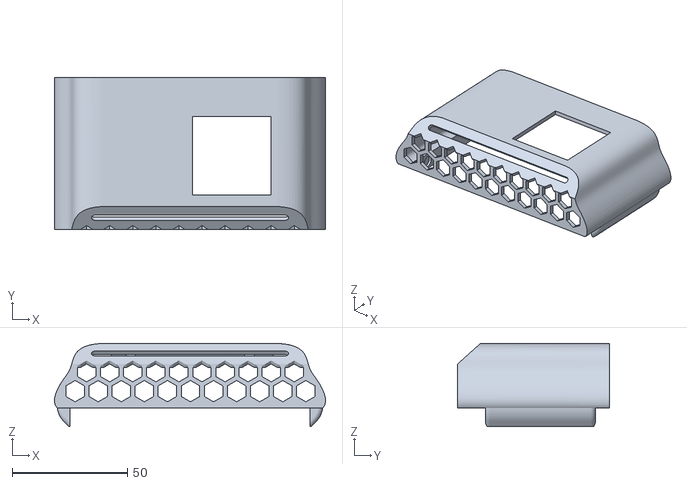
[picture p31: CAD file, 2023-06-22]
3D модели/capot_robot.stl
117.5 x 66.0 x 36.0

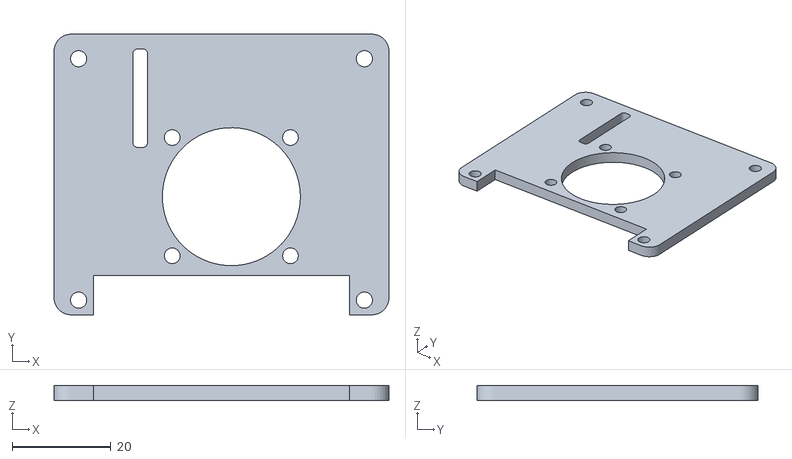
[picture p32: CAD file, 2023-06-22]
3D модели/raspberry korpus v1.stl
68.0 x 57.0 x 3.00

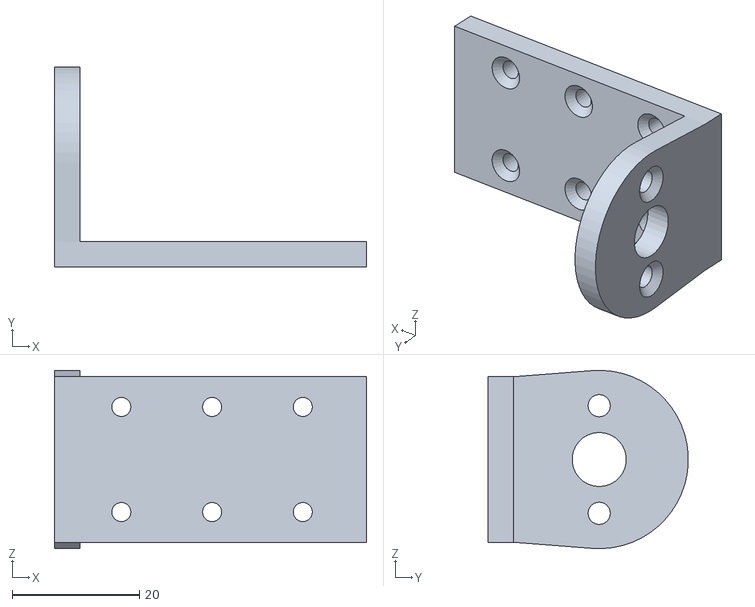
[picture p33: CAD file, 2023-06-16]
3D модели/motor_holder.stl
49.0 x 31.5 x 28.0

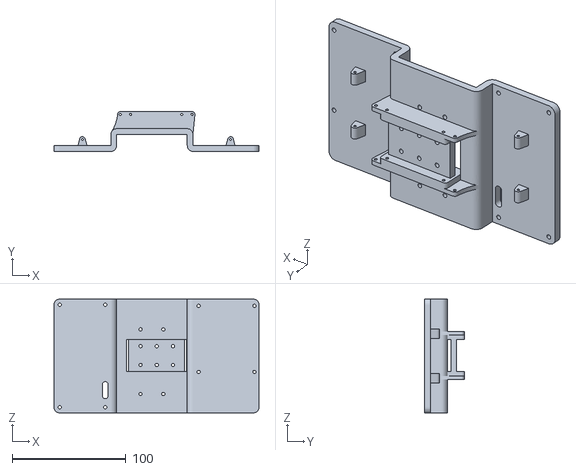
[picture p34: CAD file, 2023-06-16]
3D модели/KZAS_korpus.stl
180.0 x 35.0 x 100.0

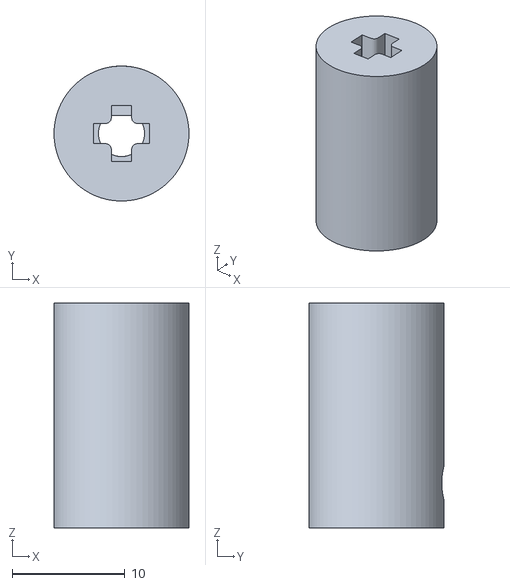
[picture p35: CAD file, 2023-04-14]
3D модели/motor_to_axle.stl
12.0 x 12.0 x 20.0

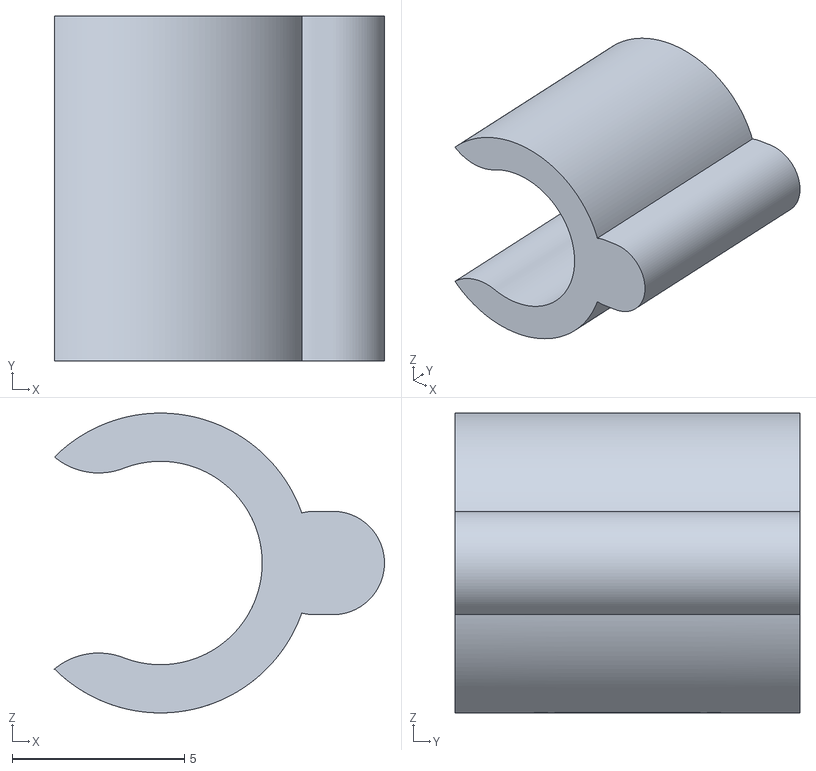
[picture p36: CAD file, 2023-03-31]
3D модели/spacer.stl
9.58 x 10.0 x 8.70

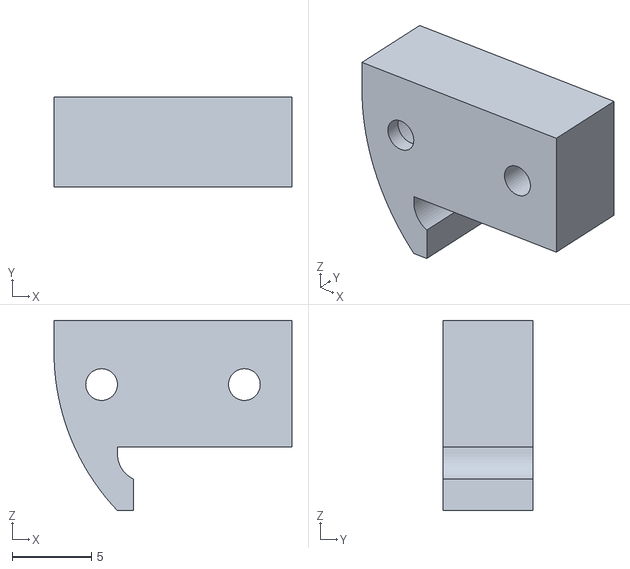
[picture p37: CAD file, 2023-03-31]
3D модели/steering_knukle.stl
15.0 x 5.70 x 12.0

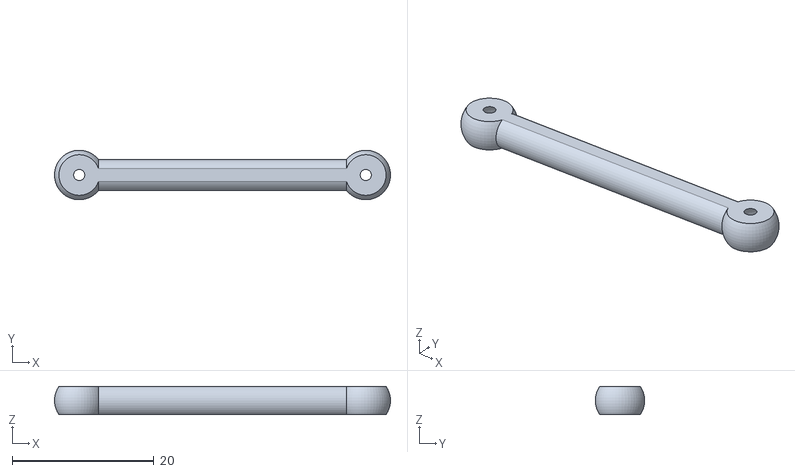
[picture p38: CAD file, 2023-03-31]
3D модели/steering_shaft.stl
47.5 x 6.99 x 4.00

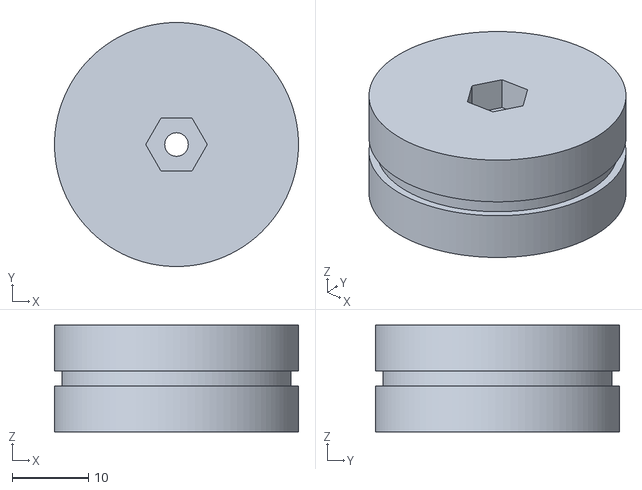
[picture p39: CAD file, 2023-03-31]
3D модели/wheel.stl
32.0 x 32.0 x 14.0

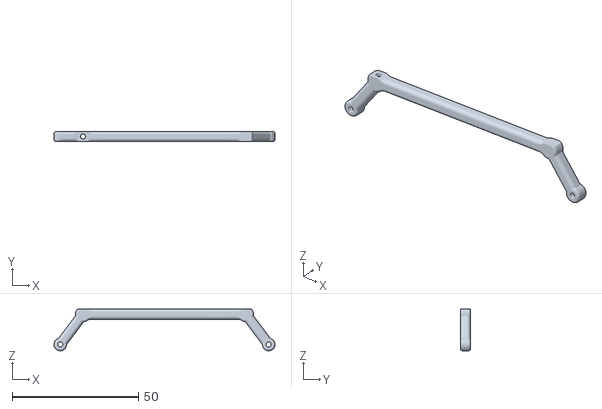
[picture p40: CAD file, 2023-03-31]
3D модели/tie_rod.stl
87.5 x 4.00 x 16.5

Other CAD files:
3D модели/bok_right.stl

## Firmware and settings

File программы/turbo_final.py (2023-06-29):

import time  # подключаем библиотеку time для работы с таймерами

import cv2  # подключаем библиотеку компьютерного зрения
import numpy as np  # подключаем библиотеку numpy
import serial  # подключаем библиотеку Serial для общения между распберри и пайбордом

import RobotAPI as Rapi  # подключаем вспомогательную библиотеку для работы с распберри

port = serial.Serial("/dev/ttyS0", baudrate=115200, stopbits=serial.STOPBITS_ONE)
robot = Rapi.RobotAPI(flag_serial=False)
robot.set_camera(100, 640, 480)

fps = 0
fps1 = 0
fps_time = 0

red = 0
green = 0
blue = 0

#  HSV для поиска цветов

lowblack = np.array([0, 151, 5])  # черный
upblack = np.array([180, 256, 71])

lowblue = np.array([80, 130, 29])  # синий
upblue = np.array([115, 255, 255])

loworange = np.array([10, 40, 50])  # оранжевый
uporange = np.array([56, 255, 255])

lowred = np.array([0, 75, 30])  # красный
upred = np.array([6, 235, 170])

lowgreen = np.array([50, 180, 64])  # зелёный
upgreen = np.array([76, 255, 255])

# координаты областей интереса
x_line_dat = [0, 220, 420, 640]  # координаты для датчиков линии
y_line_dat = [240, 280, 240, 280]

x_cross = [280, 360]  # координаты для датчика перекрёстка (оранжевой или синей линии)
y_cross = [320, 360]

x_cube = [120, 520]  # координаты для датчика кубиков (знаков)
y_cube = [200, 360]

# различные переменные для ПД регулятора
e_old = 0  # значение предыдущей ошибки для подсчёта дифференциальной составляющей
e_old_cube = 0  # значение предыдущей ошибки для подсчёта дифференциальной составляющей для регулятора для знаков
kp = 2.2  # коэффициент пропорциональной составляющей
kd = 1.2  # коэффициент дифференциальной составляющей
u = 0  # управляющее воздействие
e = 0  # ошибка (отклонение)
dat1, dat2 = [0] * 20, [0] * 20  # переменные хранящие показания датчиков линии
dat1_end, dat2_end = 0, 0

cross = 0  # счётчик перекрёсков
cross_reverse = 8
cross_finish = 12
color_line = 'none'  # цвет перекрёстка (оранжевый или синий) используется для определения направления движения
cube_color = 'none'  # цвет текущего знака (красный или зелёный)
last_cube_color = ""
last_cube_time = time.time()
timer_time = time.time()

cub_pos = 0  # индекс для списка знаков
red_pos_x = 0  # позиция красного знака по х
red_pos_y = 0  # позиция красного знака по у
green_pos_x = 0  # позиция зелёного знака по х
green_pos_y = 0  # позиция зелёного знака по у
b_g = 200  # коэффициент для подсчёта отклонения от траектроии подъезда к зелёному знаку
b_r = 200  # коэффициент для подсчёта отклонения от траектроии подъезда к красному знаку

time_finish = 0  # время для финишной зоны засечённое с помощью функции search_cross()

state = 0  # переменная состояния
tx = '99999999999999999999$'  # сообщение об ожидании кнопки
ii = '0'
stop_flag = False

# таймеры
last_cube_timer = time.time()
search_cross_time = time.time()  # таймер хранящий время последнего увиденного перекрёстка
finish_tim = time.time()  # таймер для проезда в центр финишной зоны
cube_red_exist = time.time()  # таймер исчезновения красного знака
cube_green_exist = time.time()  # таймер исчезновения зеленого знака
cube_exist_tim = time.time()  # таймер хранящий время последнего увиденного знака
reverse_timer = time.time()  # таймер для разворота
timer_timer = time.time()  # хранит время всего заезда

# флаги
flag_start = False
flag_l = False
flag_wg = True
flag_wr = True
flag_cube_exist = False
flag_sort = True
reverse_flag = True

speed = 65  # скорость
min_speed = 60
max_speed = 85
degree = 0  # угол поворота сервопривода

# списки
time_list = [0, 0, 0, 0]  # список времени зон получаемых из функции search_cross()
cub_col_list = [[0, 0, 0], [0, 0, 0], [0, 0, 0], [0, 0, 0]]  # список кубов по зонам
cub_num_list = [0, 0, 0, 0]  # список показывает сколько кубиков в каждой зоне
time_cub_list = [[0, 0, 0], [0, 0, 0], [0, 0, 0], [0, 0, 0]]  # список кубов по расположению в зоне (расчет по времени)


def black_search(d1):
    xm, ym, wm, hm = 0, 0, 0, 0
    iscontour = 0
    dat = cv2.GaussianBlur(d1, (5, 5), cv2.BORDER_DEFAULT)  # размытие фрагмента изображения
    hsv = cv2.cvtColor(dat, cv2.COLOR_BGR2HSV)  # перевод в цветовую модель HSV
    mask = cv2.inRange(hsv, lowblack, upblack)  # создание маски
    blur = cv2.blur(mask, (5, 5))  # размытие маски

    imd1, contours, hod1 = cv2.findContours(blur, cv2.RETR_TREE, cv2.CHAIN_APPROX_NONE)  # функция поиска контуров

    for contour in contours:
        x, y, w, h = cv2.boundingRect(contour)  # координаты текущего контура
        area = cv2.contourArea(contour)  # площадь текущего контура
        if area > 220:  # фильтр по минимальной площади контура
            xm, ym, wm, hm = x, y, w, h  # запись координат наибольшего контура
            iscontour = 1

    return [xm + 1, ym + 1, xm + wm - 1, ym + hm - 1, iscontour]


def detect_line_pro():
    global x_line_dat, y_line_dat, dat1, dat2, dat1_end, dat2_end

    for i in range(20):
        # забираем часть экрана для датчиков и высчитываем показания датчиков
        dat1[i] = black_search(frame[y_line_dat[0]:y_line_dat[1], i * 11:(i + 1) * 11])[4]
        dat2[i] = black_search(frame[y_line_dat[0]:y_line_dat[1], 420 + i * 11:420 + (i + 1) * 11])[4]

    dat2_end = 0
    dat1_end = 0
    for i in range(20):
        if dat2[i] == 1 and dat2_end == 0:
            dat2_end = 20 - i
        if dat1[19 - i] == 1 and dat1_end == 0:
            dat1_end = 20 - i


def draw_contour_line():  # функция для отображения датчиков и контуров
    # получаем координаты контуров
    cv2.rectangle(frame, (x_line_dat[0] - 1, y_line_dat[0] - 1), (x_line_dat[1] + 1, y_line_dat[1] + 1),
                  (255, 255, 255), 0)
    cv2.rectangle(frame, (x_line_dat[2] - 1, y_line_dat[2] - 1), (x_line_dat[3] + 1, y_line_dat[3] + 1),
                  (255, 255, 255), 0)
    for i in range(0, dat1_end):
        cv2.rectangle(frame, (i * 11, y_line_dat[0]), ((i + 1) * 11, y_line_dat[1]),
                      (0, 0, 0), -1)
    # dat2.reverse()
    for i in range(20 - dat2_end, 20):
        cv2.rectangle(frame, (420 + i * 11, y_line_dat[0]), (420 + (i + 1) * 11, y_line_dat[1]),
                      (0, 0, 0), -1)
    cv2.rectangle(frame, (x_cross[0] - 1, y_cross[0] - 1), (x_cross[1] + 1, y_cross[1] + 1),
                  (255, 255, 255), 2)
    cv2.rectangle(frame, (x_cube[0] - 1, y_cube[0] - 1), (x_cube[1] + 1, y_cube[1] + 1),
                  (255, 255, 255), 2)


def pd_regulator_cube(d1, d2, k_p=0.3, k_d=0.3):  # пропорционально-дифференциальный регулятор
    global e_old_cube, degree, color_line, u

    e = d2 - d1  # вычисяем отклонение
    if -10 < e < 10:  # если отклонение небольшое
        e = 0  # приравниваем к нулю
    u = int(e * k_p + (e - e_old_cube) * k_d)  # вычисляем управляющее воздействие по формуле ПД регулятора
    degree = u  # приравниваем угол к управляющему воздействию
    e_old_cube = e  # запоминаем предыдущую ошибку

    robot.text_to_frame(frame, e, 0, 40, (255, 255, 255), 1)


def pd_regulator(d1, d2, k_p=5.5, k_d=4.5):  # пропорционально-дифференциальный регулятор
    global e, e_old, degree, color_line, u

    e = d2 - d1  # вычисяем отклонение
    if -5 < e < 5:  # если отклонение небольшое
        e = 0  # приравниваем к нулю
    u = int(e * k_p + (e - e_old) * k_d)  # вычисляем управляющее воздействие по формуле ПД регулятора
    degree = u  # приравниваем угол к управляющему воздействию
    e_old = e  # запоминаем предыдущую ошибку

    if d1 == 0:  # если нет бортика поворачиваем в сторону где он должен быть
        degree = 45
    if d2 == 0:
        degree = -45

    if d1 == 0 and d2 == 0:  # если нет обоих бортиков поворачиваем в направлении движения
        if color_line == "orange":
            degree = -40
        elif color_line == "blue":
            degree = 40

    if d1 > 180 and d2 > 180:  # если оба датчика показывают больше 180
        if color_line == "orange":  # значит мы едем в бортик и надо срочно выруливать в направлении движения
            degree = -60
        elif color_line == "blue":
            degree = 60


def search_cross():  # функция поиска перекрёстков
    global x_cross, y_cross, lowblue, upblue, loworange, uporange, color_line, last_cube_time, cross, search_cross_time, time_finish
    dat = frame[y_cross[0]:y_cross[1], x_cross[0]:x_cross[1]]
    if color_line == 'none' or color_line == "blue":

        hsv = cv2.cvtColor(dat.copy(), cv2.COLOR_BGR2HSV)
        mask = cv2.inRange(hsv, lowblue, upblue)  #
        imd1, contours, hod1 = cv2.findContours(mask, cv2.RETR_TREE, cv2.CHAIN_APPROX_NONE)  # поиск синего перекрёстка

        for contour in contours:
            x, y, w, h = cv2.boundingRect(contour)
            a1 = cv2.contourArea(contour)
            if a1 > 450 and search_cross_time + 1.6 < time.time():
                if cross < 5:  # подсчёт времени для каждого участка трассы между перекрёстками
                    time_list[cross % 4] = round(time.time() - search_cross_time, 2)
                elif cross < 6:
                    time_finish = time_list[cross_finish % 4] * 0.6

                cv2.rectangle(dat, (x, y), (x + w, y + h), (255, 0, 0), 2)  # подсчёт перекрёстков
                if state != 0:
                    cross += 1
                    color_line = "blue"
                last_cube_time = round(time.time() - last_cube_timer, 2)
                search_cross_time = time.time()

    if color_line == 'none' or color_line == "orange":
        hsv2 = cv2.cvtColor(dat.copy(), cv2.COLOR_BGR2HSV)  # всё тоже самое только для оранжевого
        mask_d2 = cv2.inRange(hsv2, loworange, uporange)  #
        imd1, contours1, hod1 = cv2.findContours(mask_d2, cv2.RETR_TREE, cv2.CHAIN_APPROX_NONE)

        for contour1 in contours1:
            x, y, w, h = cv2.boundingRect(contour1)
            a1 = cv2.contourArea(contour1)
            if a1 > 450 and search_cross_time + 1.6 < time.time():
                if cross < 5:
                    time_list[cross % 4] = round(time.time() - search_cross_time, 2)
                elif cross < 6:
                    time_finish = time_list[0] * 0.6

                if state != 0:
                    cross += 1
                    color_line = "orange"
                last_cube_time = round(time.time() - last_cube_timer, 2)
                search_cross_time = time.time()
                cv2.rectangle(dat, (x, y), (x + w, y + h), (0, 100, 255), 2)


def print_message(sp, dg, r=0, g=0, b=0):
    lst = [str(sp + 200), str(dg + 204), str(r + 200), str(g + 200), str(b + 200), '$']  # формируем сообщение
    string = ",".join(lst)  # переводим сообщение в строку
    port.write(string.encode("utf-8"))  # отправляем сообщение


def cube_r():  # функция поиска красных кубиков
    global cube_color, cross, red_pos_x, cub_pos, red_pos_y, cube_red_exist, flag_wr, last_cube_color, last_cube_timer

    datk1 = frame[y_cube[0]:y_cube[1], x_cube[0]:x_cube[1]]
    hsv = cv2.cvtColor(datk1, cv2.COLOR_BGR2HSV)
    mask = cv2.inRange(hsv, lowred, upred)
    blur = cv2.blur(mask, (5, 5))
    imd1, contours, hod1 = cv2.findContours(blur, cv2.RETR_TREE, cv2.CHAIN_APPROX_NONE)

    xm, ym, wm, hm = 0, 0, 0, 0

    if len(contours) != 0:
        max = 0
        for contor in contours:
            x, y, w, h = cv2.boundingRect(contor)
            area = cv2.contourArea(contor)
            if area > 450:
                cube_red_exist = time.time()
                if y + h > max:  # поиск наибольшего
                    max = y + h
                    xm, ym, wm, hm = x, y, w, h

            else:
                if cube_red_exist + 0.15 < time.time():  # таймер для исчезновения кубика
                    xm, ym, wm, hm = 0, 0, 0, 0
        if ym + hm > 100 and flag_wr and 0 < cross < 5:  # запись кубиков в список
            flag_wr = False
            cub_col_list[cross % 4][cub_pos % 3] = 'r'
            time_cub_list[cross % 4][cub_pos % 3] = round(time.time() - search_cross_time, 1)
            cub_pos += 1
        if ym + hm < 60 and not flag_wr:
            flag_wr = True
        if max > 155:
            last_cube_color = "red"
            last_cube_timer = time.time()

    else:
        if cube_red_exist + 0.15 < time.time():
            xm, ym, wm, hm = 0, 0, 0, 0

    return [xm + 1, ym + 1, xm + wm - 1, ym + hm - 1]


def cube_g():  # функция поиска зеленых кубиков (за подробностями в cube_R())
    global green_pos_x, green_pos_y, cube_green_exist, flag_wg, cub_pos, last_cube_color, last_cube_timer

    datg1 = frame[y_cube[0]:y_cube[1], x_cube[0]:x_cube[1]]
    hsv = cv2.cvtColor(datg1, cv2.COLOR_BGR2HSV)
    mask = cv2.inRange(hsv, lowgreen, upgreen)
    blur = cv2.blur(mask, (5, 5))
    imd1, contoursk, hod1 = cv2.findContours(blur, cv2.RETR_TREE, cv2.CHAIN_APPROX_NONE)
    max = 0

    xm, ym, wm, hm = 0, 0, 0, 0

    if len(contoursk) != 0:
        for contork1 in contoursk:
            x, y, w, h = cv2.boundingRect(contork1)
            area = cv2.contourArea(contork1)
            if area > 400 and h / w > 1:

                cube_green_exist = time.time()
                if y + h > max:
                    max = y + h
                    xm, ym, wm, hm = x, y, w, h
            else:
                if cube_green_exist + 0.15 < time.time():
                    xm, ym, wm, hm = 0, 0, 0, 0
        if ym + hm > 100 and flag_wg and 0 < cross < 5:
            cub_col_list[cross % 4][cub_pos % 3] = 'g'
            flag_wg = False
            time_cub_list[cross % 4][cub_pos % 3] = round(time.time() - search_cross_time, 1)
            cub_pos += 1
        if ym + hm < 50 and not flag_wg:
            flag_wg = True
        if max > 155:
            last_cube_color = "green"
            last_cube_timer = time.time()
    else:
        if cube_green_exist + 0.15 < time.time():
            xm, ym, wm, hm = 0, 0, 0, 0

    return [xm + 1, ym + 1, xm + wm - 1, ym + hm - 1]


def state_changer():
    global state
    key = robot.get_key()

    if key != -1:
        if key == 48:
            state = 0
        elif key == 49:
            state = 1
        elif key == 50:
            state = 2
        elif key == 51:
            state = 3
        elif key == 52:
            state = 4
        elif key == 53:
            state = 5


def max_min_index(list_i):
    max_i = 0
    min_i = 0
    for i in range(len(list_i)):
        if list_i[max_i] < list_i[i]:
            max_i = i
        if list_i[min_i] > list_i[i]:
            min_i = i
    return max_i, min_i


def cub_list_sort():
    global time_list, cub_num_list, cub_col_list, time_cub_list
    for i in range(4):
        for j in range(3):
            if cub_col_list[i][j] != 0:
                cub_num_list[i] += 1

    for i in range(4):
        if cub_num_list[i] == 2:
            max_i, min_i = max_min_index(time_cub_list[i])
            time_cub_list[i][max_i], time_cub_list[i][2] = time_cub_list[i][2], time_cub_list[i][max_i]
            cub_col_list[i][max_i], cub_col_list[i][2] = cub_col_list[i][2], cub_col_list[i][max_i]
            max_i, min_i = max_min_index(time_cub_list[i])
            if min_i != 1:
                time_cub_list[i][min_i], time_cub_list[i][1] = time_cub_list[i][1], time_cub_list[i][min_i]
                cub_col_list[i][min_i], cub_col_list[i][1] = cub_col_list[i][1], cub_col_list[i][min_i]

        elif cub_num_list[i] == 1:
            max_i, min_i = max_min_index(time_cub_list[i])
            if time_cub_list[i][max_i] <= 0.6:
                time_cub_list[i][max_i], time_cub_list[i][0] = time_cub_list[i][0], time_cub_list[i][max_i]
                cub_col_list[i][max_i], cub_col_list[i][0] = cub_col_list[i][0], cub_col_list[i][max_i]
            elif time_cub_list[i][max_i] <= 1.2:
                time_cub_list[i][max_i], time_cub_list[i][1] = time_cub_list[i][1], time_cub_list[i][max_i]
                cub_col_list[i][max_i], cub_col_list[i][1] = cub_col_list[i][1], cub_col_list[i][max_i]
            else:
                time_cub_list[i][max_i], time_cub_list[i][2] = time_cub_list[i][2], time_cub_list[i][max_i]
                cub_col_list[i][max_i], cub_col_list[i][2] = cub_col_list[i][2], cub_col_list[i][max_i]


def reverse():
    global speed, degree, color_line, state, time_finish, cross
    if color_line == "blue":
        if last_cube_time > 0.6:
            if reverse_timer + 1.4 > time.time():
                speed = 30
                degree = -60
            elif reverse_timer + 1.4 + 1.2 > time.time():
                speed = -30
                degree = 60
            elif reverse_timer + 1.4 + 1.2 + 0.5 > time.time():
                speed = 30
                degree = -30
            else:
                state = 4
                speed = 40
                color_line = "orange"
        else:
            if reverse_timer + 1.1 > time.time():
                speed = 30
                degree = 60
            elif reverse_timer + 1.1 + 1.4 > time.time():
                speed = -30
                degree = -60
            elif reverse_timer + 1.1 + 1.4 + 0.3 > time.time():
                speed = -20
                degree = 30
            else:
                state = 4
                speed = 40
                time_finish += 0.4
                color_line = "orange"
    elif color_line == "orange":
        if reverse_timer + 1.7 > time.time():
            speed = 30
            degree = 55
        elif reverse_timer + 1.7 + 1.3 > time.time():
            speed = -30
            degree = -60
        elif reverse_timer + 1.7 + 1.3 + 0.5 > time.time():
            if last_cube_time > 0.6:
                speed = 20
            else:
                speed = -20
            degree = 0
        else:
            state = 4
            time_finish += 0.2
            speed = 40
            color_line = "blue"


def axeleration():
    global speed
    if cube_exist_tim + 0.3 < time.time():
        if speed < max_speed:
            speed += 0.5
        elif speed > max_speed:
            speed = max_speed
    else:
        if speed > min_speed:
            speed -= 0.5
        elif speed < min_speed:
            speed += 0.1


green_pos = None
red_pos = None
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

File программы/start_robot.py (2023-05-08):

# pyinstaller --onefile --noconsole start_robot.py
__author__ = 'Yuri Glamazdin <yglamazdin@gmail.com>'
__version__ = '1.6'

import json
import os
import socket as sc
import threading
import time
import tkinter.filedialog as tkFileDialog
import tkinter as tk
import cv2
import numpy as np
import zmq
import zlib
import base64
import InetConnection as InetConnection
# Create a UDP socket
import select

from ctypes import *
from ctypes.util import find_library
import platform
import numpy as np
import math
import warnings
import os
import pickle, base64

flag_udp_comand = False
flag_udp_event = False
flag_udp_turbo_show_window = False
flag_udp_show_window = False

show_system_message = False
fps_fix_timer = 0.04


video_show = 0
video_show2 = 3
video_show2_global = 0
video_show2_global = 0
video_show_work = False
flag_start_script = None
timer_wait_start = 10
lock_time = 10+60 * 30

# default libTurboJPEG library path
DEFAULT_LIB_PATHS = {
    'Darwin': ['/usr/local/opt/jpeg-turbo/lib/libturbojpeg.dylib'],
    'Linux': [
        '/usr/lib/x86_64-linux-gnu/libturbojpeg.so.0',
        '/opt/libjpeg-turbo/lib64/libturbojpeg.so'
    ],
    # 'Windows': ['C:/libjpeg-turbo-gcc64/bin/libturbojpeg.dll']
    'Windows': ['libturbojpeg.dll']
}

# error codes
# see details in https://github.com/libjpeg-turbo/libjpeg-turbo/blob/master/turbojpeg.h
TJERR_WARNING = 0
TJERR_FATAL = 1

# color spaces
# see details in https://github.com/libjpeg-turbo/libjpeg-turbo/blob/master/turbojpeg.h
TJCS_RGB = 0
TJCS_YCbCr = 1
TJCS_GRAY = 2
TJCS_CMYK = 3
TJCS_YCCK = 4

# pixel formats
# see details in https://github.com/libjpeg-turbo/libjpeg-turbo/blob/master/turbojpeg.h
TJPF_RGB = 0
TJPF_BGR = 1
TJPF_RGBX = 2
TJPF_BGRX = 3
TJPF_XBGR = 4
TJPF_XRGB = 5
TJPF_GRAY = 6
TJPF_RGBA = 7
TJPF_BGRA = 8
TJPF_ABGR = 9
TJPF_ARGB = 10
TJPF_CMYK = 11

# chrominance subsampling options
# see details in https://github.com/libjpeg-turbo/libjpeg-turbo/blob/master/turbojpeg.h
TJSAMP_444 = 0
TJSAMP_422 = 1
TJSAMP_420 = 2
TJSAMP_GRAY = 3
TJSAMP_440 = 4
TJSAMP_411 = 5

# miscellaneous flags
# see details in https://github.com/libjpeg-turbo/libjpeg-turbo/blob/master/turbojpeg.h
# note: TJFLAG_NOREALLOC cannot be supported due to reallocation is needed by PyTurboJPEG.
TJFLAG_BOTTOMUP = 2
TJFLAG_FASTUPSAMPLE = 256
TJFLAG_FASTDCT = 2048
TJFLAG_ACCURATEDCT = 4096
TJFLAG_STOPONWARNING = 8192
TJFLAG_PROGRESSIVE = 16384


class TurboJPEG(object):
    """A Python wrapper of libjpeg-turbo for decoding and encoding JPEG image."""

    def __init__(self, lib_path=None):
        turbo_jpeg = cdll.LoadLibrary(
            self.__find_turbojpeg() if lib_path is None else lib_path)
        self.__init_decompress = turbo_jpeg.tjInitDecompress
        self.__init_decompress.restype = c_void_p
        self.__init_compress = turbo_jpeg.tjInitCompress
        self.__init_compress.restype = c_void_p
        self.__destroy = turbo_jpeg.tjDestroy
        self.__destroy.argtypes = [c_void_p]
        self.__destroy.restype = c_int
        self.__decompress_header = turbo_jpeg.tjDecompressHeader3
        self.__decompress_header.argtypes = [
            c_void_p, POINTER(c_ubyte), c_ulong, POINTER(c_int),
            POINTER(c_int), POINTER(c_int), POINTER(c_int)]
        self.__decompress_header.restype = c_int
        self.__decompress = turbo_jpeg.tjDecompress2
        self.__decompress.argtypes = [
            c_void_p, POINTER(c_ubyte), c_ulong, POINTER(c_ubyte),
            c_int, c_int, c_int, c_int, c_int]
        self.__decompress.restype = c_int
        self.__compress = turbo_jpeg.tjCompress2
        self.__compress.argtypes = [
            c_void_p, POINTER(c_ubyte), c_int, c_int, c_int, c_int,
            POINTER(c_void_p), POINTER(c_ulong), c_int, c_int, c_int]
        self.__compress.restype = c_int
        self.__free = turbo_jpeg.tjFree
        self.__free.argtypes = [c_void_p]
        self.__free.restype = None
        self.__get_error_str = turbo_jpeg.tjGetErrorStr
        self.__get_error_str.restype = c_char_p
        # tjGetErrorStr2 is only available in newer libjpeg-turbo
        self.__get_error_str2 = getattr(turbo_jpeg, 'tjGetErrorStr2', None)
        if self.__get_error_str2 is not None:
            self.__get_error_str2.argtypes = [c_void_p]
            self.__get_error_str2.restype = c_char_p
        # tjGetErrorCode is only available in newer libjpeg-turbo
        self.__get_error_code = getattr(turbo_jpeg, 'tjGetErrorCode', None)
        if self.__get_error_code is not None:
            self.__get_error_code.argtypes = [c_void_p]
            self.__get_error_code.restype = c_int
        self.__scaling_factors = []

        class ScalingFactor(Structure):
            _fields_ = ('num', c_int), ('denom', c_int)

        get_scaling_factors = turbo_jpeg.tjGetScalingFactors
        get_scaling_factors.argtypes = [POINTER(c_int)]
        get_scaling_factors.restype = POINTER(ScalingFactor)
        num_scaling_factors = c_int()
        scaling_factors = get_scaling_factors(byref(num_scaling_factors))
        for i in range(num_scaling_factors.value):
            self.__scaling_factors.append(
                (scaling_factors[i].num, scaling_factors[i].denom))

    def decode_header(self, jpeg_buf):
        """decodes JPEG header and returns image properties as a tuple.
           e.g. (width, height, jpeg_subsample, jpeg_colorspace)
        """
        handle = self.__init_decompress()
        try:
            width = c_int()
            height = c_int()
            jpeg_subsample = c_int()
            jpeg_colorspace = c_int()
            jpeg_array = np.frombuffer(jpeg_buf, dtype=np.uint8)
            src_addr = self.__getaddr(jpeg_array)
            status = self.__decompress_header(
                handle, src_addr, jpeg_array.size, byref(width), byref(height),
                byref(jpeg_subsample), byref(jpeg_colorspace))
            if status != 0:
                self.__report_error(handle)
            return (width.value, height.value, jpeg_subsample.value, jpeg_colorspace.value)
        finally:
            self.__destroy(handle)
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

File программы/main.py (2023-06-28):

from pyb import delay, Pin, ADC, Timer, UART
import pyb  # импортируем внутреннюю библиотеку пайборда

# настраиваем UART(протокол общения между pyboard и raspberry
uart = UART(2, 115200, stop=1)  # пин для UART
inn = ''

# задаём пины для работы
servo = pyb.Servo(1)  # пин для сервопривода
servo.angle(-8)  # поворот сервы в 0 градусов

RED = pyb.LED(1)
GREEN = pyb.LED(2)  # пины для встроенных светодиодов пайборда
YELLOW = pyb.LED(3)
BLUE = pyb.LED(4)

p_in = Pin('X10', Pin.IN, Pin.PULL_UP)  # пин кнопки

Ma = Pin('Y10', Pin.OUT_PP)  # пины для работы с драйвером
Mb = Pin('Y9', Pin.OUT_PP)

Sp = Pin('X8')  # пин скорости является ШИМ пином
tim = Timer(14, freq=10000)
ch = tim.channel(1, Timer.PWM, pin=Sp)

# пины для RGB светодиода
Spr = Pin('Y8')
tim = Timer(1, freq=2000)
r = tim.channel(3, Timer.PWM, pin=Spr)
Spg = Pin('Y6')
tim = Timer(1, freq=2000)
g = tim.channel(1, Timer.PWM, pin=Spg)
Spb = Pin('Y7')
tim = Timer(1, freq=2000)
b = tim.channel(2, Timer.PWM, pin=Spb)


def RGB_LED(red, green, blue):
    r.pulse_width_percent(red)
    g.pulse_width_percent(green)
    b.pulse_width_percent(blue)


def motor(sped):  # функция упрощённого управления мотором
    global Ma, Mb, ch
    if sped > 0:
        Ma.low()
        Mb.high()
        ch.pulse_width_percent(sped)
    else:
        Mb.low()
        Ma.high()
        ch.pulse_width_percent(abs(sped))


def decrypt(strin):
    total = [0, 0, 0, 0, 0]
    lst = strin.split(',')
    for i in range(5):
        total[i] = int(lst[i]) - 200
    return total


message = ""
flag_start = False
YELLOW.off()
a = 0

for i in range(100):
    RGB_LED(i, 100 - i, 0)
    delay(10)
servo.angle(-60)
for i in range(100):
    RGB_LED(100 - i, 0, i)
    delay(10)
servo.angle(60)
for i in range(100):
    RGB_LED(0, i, 100 - i)
    delay(10)
servo.angle(0)

while 1:
    if uart.any():  # обработка сообщений
        YELLOW.on()
        a = chr(uart.readchar())  # посимвольное чтение сообщение
        if a != '$':  # если не обгаружен стоп-символ
            inn += a  # добавляем символ к сообщению
            if len(inn) > 20:  # отсечение по длине (если сообщение длиннее чем должно быть то мы его игнорируем)
                inn = ""
        else:
            if not flag_start:  # сообщение "99999999999999999999" говорит о том что распберри запустилась
                if inn == "99999999999999999999":
                    flag_start = True
                    BLUE.on()  # как индикация включается синий светодиод
                    RGB_LED(99, 99, 99)  # и RGB светодиод горит белым
            else:
                message = str(p_in.value()) + '$'  # формируем сообщение с показанием кнопки
                try:
                    if inn != '99999999999999999999' and len(inn) == 20:  # чтение сообщения и езда
                        print(inn)
                        spisok = decrypt(inn)  # читаем сообщение и разбиваем его на список
                        speed = int(spisok[0])  # из списка с сообщением достаём скорость и угол поворота
                        rul = int(spisok[1])
                        rul = -rul  # угол поворота инвертируем только если необходимо
                        #             (это обусловлено конструкцией)
                        if rul > 60:  # ограничение угла поворота
                            rul = 60
                        if rul < -60:
                            rul = -60
                        RGB_LED(spisok[2], spisok[3], spisok[4])  # из списка с сообщением достаём цвет светодиода
                        motor(speed)  # запускаем мотор со скоростью из сообщения
                        servo.angle(rul)  # поворачиваем сервопривод на заданный угол
                        # rul - 8 нужно для того, чтобы угол сервы совпадал с 0 переменной rul
                    else:
                        RGB_LED(99, 99, 99)
                        print(inn)
                except ValueError:
                    print("err")

            inn = ""
            uart.write(message)  # отсылаем показания кнопки
    else:
        YELLOW.off()

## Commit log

2022-05-12 ыфвфы
2023-03-04 жеточайше написал новый алгоритм общения
2023-03-05 квала за 18 сек на легчайшей расстановке
2023-03-05 надо допилить (квала с расширением работает неоч
2023-03-09 жёстко напеределывал
2023-03-10 квала - фул , финал - тока начали
2023-03-11 перевёл README
2023-03-11 поправил
2023-03-12 поправил ещё раз
2023-03-31 залил все модели
    [KZAS_BUMP.stl, KZAS_BUMP_SAS.stl, KZAS_camera165.stl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]
2023-04-16 Update питание и сенсоры.txt
2023-04-16 Create да
2023-04-16 Update ходовая часть.txt
2023-05-09 обновил часть документации
2023-05-09 Update README.md
    исправлено несколько опечаток
2023-05-09 Документация к программе
    доделал
2023-05-18 выложил новый корпус кирилл пж чекни
    [corpus.stl]
2023-06-17 Документация к программе (нужно докинуть фоток)
2023-06-22 детали обшивки робота
    [back_bumper.stl, bok_left.stl, bok_right.stl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]
